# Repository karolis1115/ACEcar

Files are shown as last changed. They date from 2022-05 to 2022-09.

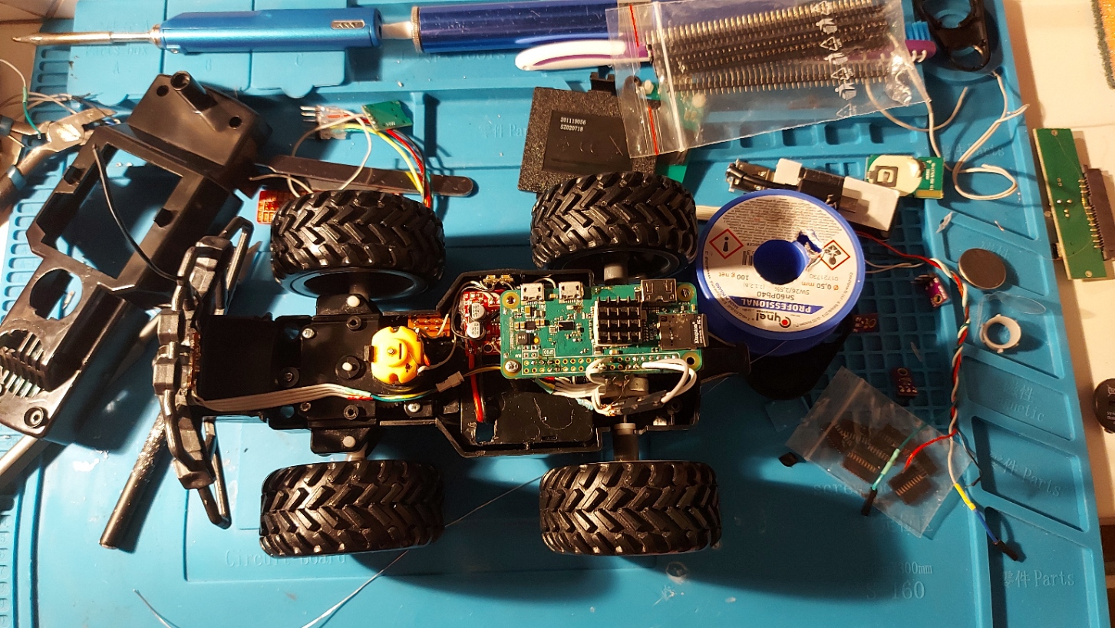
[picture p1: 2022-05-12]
Pictures and videos/20220318_200529.jpg

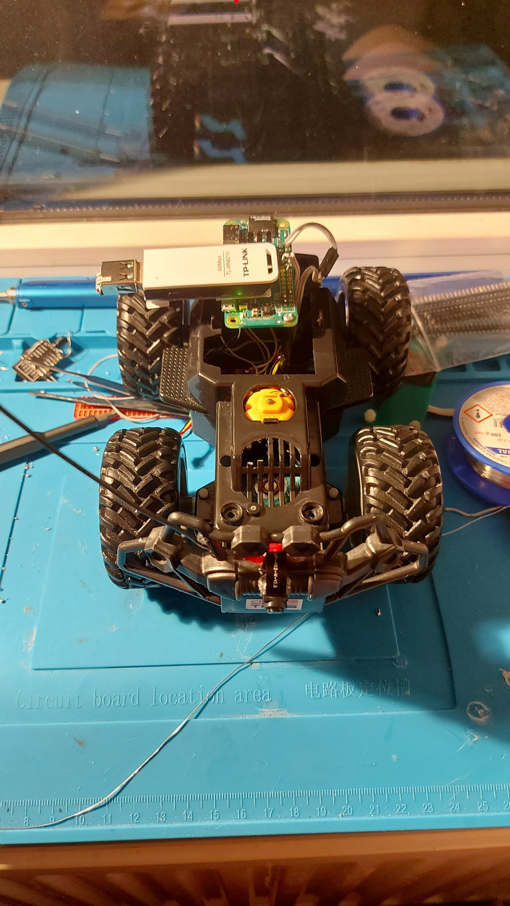
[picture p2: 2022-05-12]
Pictures and videos/20220318_201231.jpg

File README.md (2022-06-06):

# ACEcar
Saxion University of Applied Sciences Project System 2022 ACEcar repo. 

# Team members
- Miguel Pérez Hernández: 524262
- Karolis Juozapaitis: 517546
- Jurijs Zuravlovs: 440882
- Dmytro Taras: 516824
- Tarik Mandic: 523830

# Goal
To make an autonomous car that follows a line and avoids obstacles using a camera (Plan B is to use an ultrasonic sensor and light sensor array).

# What is what
- ACEcar - Main folder where main code is
- Altium files - Schematics, PCB, Gerber and other files
- Arduino test files - Files for testing different functions whre an arduino is required.
- Component sktetches - Component 3d models and sketches
- Documents - Files such as Reports and project plans and so on
- PC test files - Files for testing different functions for pc side
- Pictures - Project pictures and so on
- Raspberry pi setup - Text files that contain commands + config strings to prepare  the raspberry pi to funtion correctly for the desired requirements
- Raspberry pi test files - Files for testing different functions for pi side.

# Raspberry Pi pin configuration
- Monster Moto Driver
  - INA- 5
  - INB- 6
  - Drive (PWM1)- 12
  - Steer (SPWM)- 13

- UART
  - UART TX- 14
  - UART RX- 15

- 8x IR Line Tracking Module
  - IR- 16
  - D1-D8 -> ADC

- ADC0,1
   - SPI: 7, 8, 9, 10, 11
   - GPIO 7- CS1
   - GPIO 8- CS0

- Ultrasonic
  - Trig- 20
  - Echo- 21

# Sources
  OpenCV- https://github.com/opencv/opencv

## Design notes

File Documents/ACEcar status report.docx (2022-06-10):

ACEcar status report

This document contains a list of explanations on what has changed since the 2022 Project system race.

# Electronics

## Camera and/or cable

During the race after the car stopped video feed was lost, attempt to reestablish video feed was unsuccessful, upon closed inspection camera is missing components, due to the stress that the cable was it is also possible that the cable was damaged (however multimeter did not find any broken connections)

## Servo motors

During the development of the car, we had to replace the servo motor, the broken one is included in the box.

## Main board

for demonstration and race a PCB was not used, all connections were made manually with headers and wires, this is no longer the case as the Ordered PCB has been received, soldered and tested and is working fine after a small modification (added a capacitor to servo power pin due to voltage spikes triggering buck converter safety and shutting down the system).

P.S. Components and wires used before are contained in the box

# Cosmetic

## Frame

During the race the frame was damaged, the front bumper and back was damaged, however our team quickly repaired the broken areas and were mostly able to restore the car to its original glory.

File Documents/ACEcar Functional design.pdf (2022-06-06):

# Functional Design (FD)

# Project: Autonomous Race car

# Company: ACEcar

Place, date: Enschede, 12th February 2022

Drawn up by: Jurijs Zuravlovs
| Dmytro Taras Karolis Juozapaitis Tarik Mandic Miguel Pérez Hernández
Version: | 1.1

Drawn up by: Ali Yuksel

Place, date: | Enschede, 4.03.2022
Prepared by: | ACEcar
| Miguel Pérez Hernández | 524262 | 524262@student.saxion.nl
| Tarik Mandic | 523830 | 523830@student.saxion.nl
| Karolis Juozapaitis | 517546 | 517546@student.saxion.nl
| Dmytro Taras | 516824 | 516834@student.saxion.nl
| Jurijs Zuravlovs | 440882 | 440882@student.saxion.nl
Version number: | [1.1]
Clients: | A. Yuksel, A. Fiselier, Y. Kasemsinsup

Functional Design | version no: | iii

## Table of Contents

Functional Design | version no: | iv

## I. List of figures

Figure 1 Project management | Error! Bookmark not defined.
Figure 2 XKCD graph: walking back to my front door at night | Error! Bookmark not defined.

Functional Design | version no: | v

## II. Abbreviations

SBC
DSP | Digital Signal Processing
FFT | Fast Fourier Transform
TL;DR | Too long didn’t read
SBC | Single Board Computer

Functional Design | version no: | 1

1 Introduction.

The goal of the project is to build a car which will be follow a line. The car is moving due to hardware and software interweaving. Final product is a fully autonomous car which is following the line. The main idea is to use a sensor which takes the light and due to processing the car moves forward by the line. If the line turns the processor which see that the line is turned rotate the wheels and making the car to drive in a certain direction.

Goal of this document is to show the functional design of this project explain some basic ideas and show the concepts of a car. In this document description of a software and hardware part is provided below. Also, this document provides a requirement analysis and electronics part of the project. Therefore, the concepts and management also provided. All information this document includes can be found above.

## 2 Analysis of requirements

Requirements settled by stake holder

Requirement | Approach
1. Ride autonomously. | Create a program that will guide itself with the response of the sensors data
2. Work for at least 30 minutes. | Make sure by calculation and measurements the electric features and specifications that it will perform to that standard.
3. fit in a box of 400mm x 250mm x 200mm. | Create a model of the car respecting this dimension
4. Follow the track line (20mm). | Have sensors in order to track the line
5. Stop at the end of the track. | Figure out a way to know when the car reaches the end of the line and tell the code to terminate the program
6. Avoid obstacles. | Include sensors to have feedback if an obstacle is found in its path and be able to respond to it with an appropriate action (For ex: drive around the obstacle)
7. Find the track line. | Use input from sensors or a camera to find and track the line
8. have a body (3D printed separate parts). | Create a 3d model which will be possible to attach to the main body of the RC car.

Requirements settled by our team.

Requirement | Approach
1. Cost efficient | Calculate beforehand and produce a budget with a margin of price tolerance
2. Environmentally friendly project. | Make sure the parts used are as eco-friendly as possible like recycled printing polysynthetic
3. Development under our current knowledge | Know the team skills and knowledge to make sure the project is not too ambitious

## 3 Concept Principles

Morphological overview

Drive Mechanism | Front wheel drive | Rear wheel drive | Free wheel chain drive | 4x4 wheel drive
Processing platform | FPGA | Microcontroller | PLC | PC | Raspberry Pi
Sensor | Acoustic | optic | IR (Infrared)
Sensor amount | 1 | 2 | 3 | 4 | 5
Motor type | linear | Rotating DC | Rotating AC | stepper | Servo
Motor amount | 1 | 2
Storage | Battery | capacitor | Capacitor and battery
Car body | Pick-up truck | minivan | Convertible | Sports car | coupe

### 3.1 Description of alternative concepts

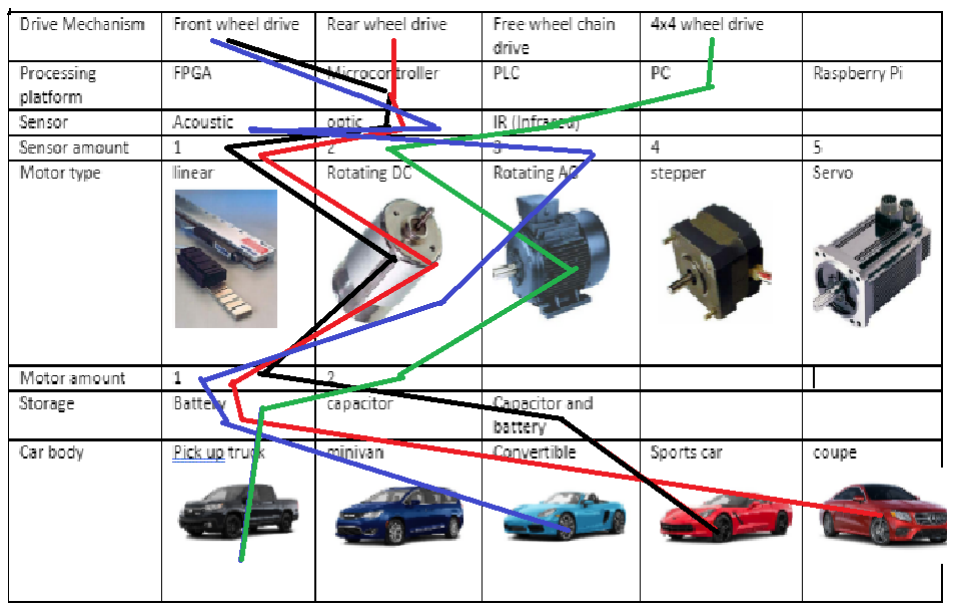
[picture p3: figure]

With the morphological overview, 4 different concepts were made.

1. Black
- Front wheel drive
- Microcontroller
- 1 Optic sensor
- 1 DC motor
- Capacitor & Battery
- Sports car
2. Red
- Rear wheel drive
- Microcontroller
- 1 Optic sensor
- 1 DC motor
- Battery
- Coupe
3. Green
- Four-wheel drive
- PC
- 2 IR (infrared)
- 2 AC motors
- Battery
- Pick-up truck
4. Blue
- Front wheel drive
- Microcontroller
- 3 sensors for either Optic & Acoustic
- 1 DC motor
- Battery
- convertible

Some comprehensive concepts:

5. Using an Arduino and a light sensor to see when it goes out of track and correct itself + an ultrasonic sensor to detect any obstacles (The simplest concept so far).
6. Using an Arduino/microcontroller with a light sensor array to detect the track and an ultrasonic sensor or rangefinder for obstacle detection/avoidance.
7. Using a raspberry pi with a camera and OpenCV to detect the track and depending on where the camera is mounted also detect the obstacles or use another distance sensor (rangefinder, ultrasonic) Demo: https://lejosnews.wordpress.com/2015/12/03/line-following-with-opencv/
8. Using a mini drone that has a camera and can stream video and be controlled over Wi-Fi for visual data which then a raspberry pi or a computer could calculate where the car and drone should drive/ fly (using OpenCV and ArUco markers) (the problem is the drone can only fly for +-5 minutes after fully charged so it would probably need to be wired up with a long but light cable) have the drone video stream and control working.

### 3.2 Comparison of concept principles

The difference between concepts 1 and 2 are the FWD and RWD and capacitor. The RWD is better because the sensor is placed in the front of the car, needing a better weight balance by putting the motor at the back. The capacitor will not be a good option for the RWD as the traction might be lost during the speed up. So, combining the capacitor with the FWD is better.

The 3rd concept is hard to do because of the processing with the PC, it is not clear how the communication will be done between the car and the PC.

The 4th concept is good, but with the Four WD, with only 1 DC motor will miss the option to add more speed to the car with the increased control that four WD allows.

### 3.3 Choice of most promising concept principle

A combination of the combination is the best.

- Four-wheel drive
- Microcontroller
- 3 sensors for either Optic & Acoustic
- 2 DC motor
- Battery
- convertible

## 4 Elaboration of chosen principle to functional design

### 4.1 Overview of functional design

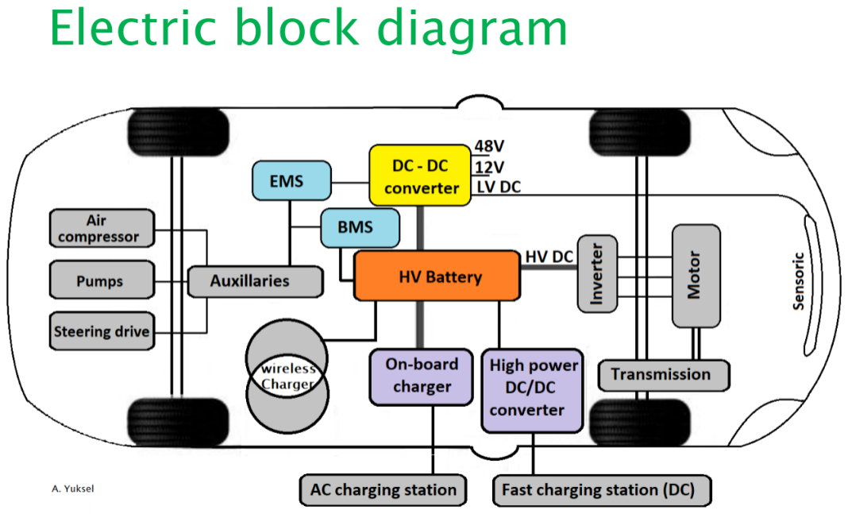
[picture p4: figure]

### 4.2 Elaboration of functional design

4.2.1 Mechanical
Base frame: ISH‑010

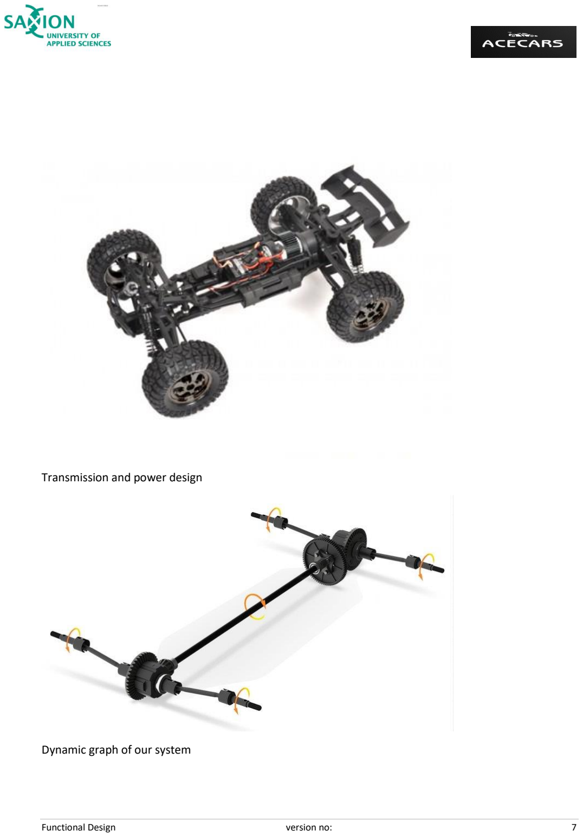
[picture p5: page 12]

Transmission and power design

Dynamic graph of our system

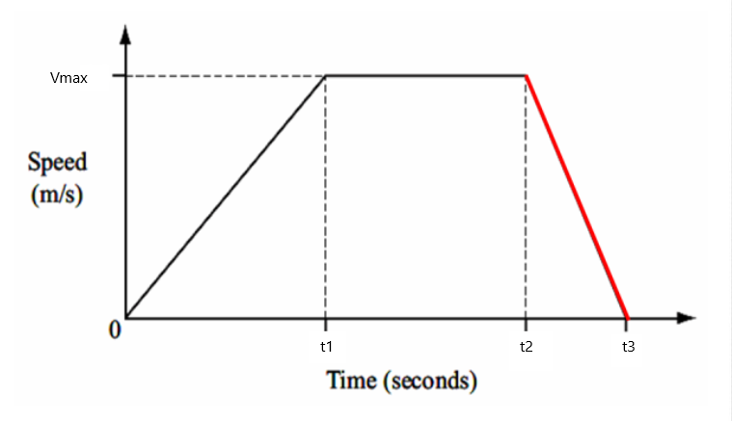
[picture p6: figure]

4.2.2 Electrical

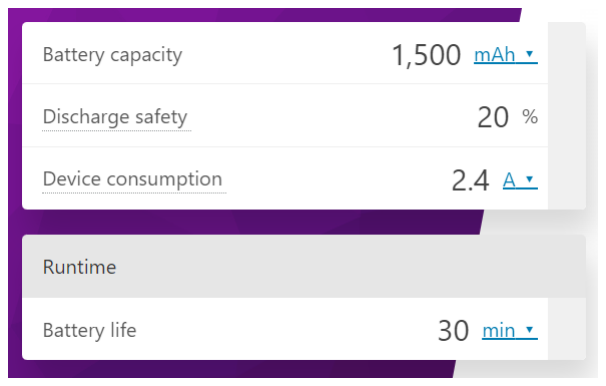
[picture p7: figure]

Battery: Li-ion 2s 1p 7.4v 1500mAh

Discharge safety: 20% (The percentage left that is considered “fully discharged” to protect the battery from over discharge may be possible to go a bit lower but a lithium-ion (Li-ion) battery cannot be discharged below 2.5 volts and a lithium polymer (Li-Po) battery cannot be discharged below 3 volts, or battery damage will occur!).

Without Risking over-discharge, we could draw 2.5A continuously to get 30 minutes of power (if discharging 80% of the battery’s capacity)

Voltage conversions:

- Battery charger ->7.4v Li-Po
- 7.4v Li-ion -> Step-down converter (5v, 3.3v, …)
- 7.4v Li-ion-> Motor driver-> Motor(s)
- Step-down converter 5v-> Raspberry Pi, servo motor, Arduino, Camera, sensors…
- Step-down converter 3.3v-> Sensors

4.2.3 Electronic
- If we choose PC, we’d need to find a way to communicate control data and sensor/ video data between the car and PC. Potentially requiring a raspberry pi anyway. This might be a good option if we’re going to need quite a bit more processing power than a raspberry pi can provide.
- If we choose a raspberry pi or similar single board computer everything could be connected locally, and we’d interface with the SBC through Wi-Fi or Bluetooth using SSH (Secure Shell Connect)
- If we use an Arduino (Meaning we’d only use sensors) we wouldn’t need any way of wireless communication since the Arduino communicates through a USB to Serial chip meaning a USB cable is all that is needed to communicate with it and upload code, we could use a button to start the car or simply add a delay from when the battery was connected.
- Using a Camera for visual data would allow to use a single sensor (the camera) for line detection, obstacle avoidance and stopping at the end of the road. The capture rate would depend on the camera and the processing power.
- Using a light sensor array would make it simpler to implement everything but would also require the use of a distance sensor (ultrasonic, laser ranging (ToF), button…)

4.2.4 Software

- Actor – Critic algorithm for self – driving cars.
- In image processing, line detection algorithm - the Hough transform and convolution-based techniques.
- Architecture diagram with modules and interfaces.

Software Block diagram [1]

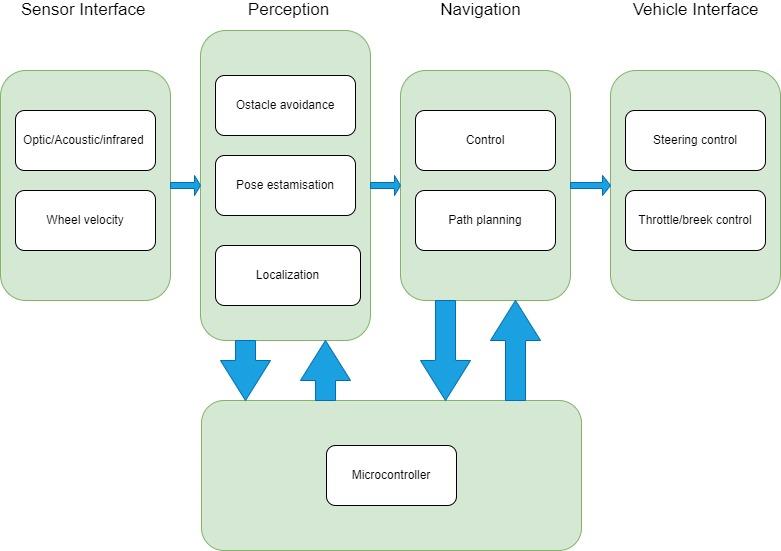
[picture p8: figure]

System states plus state transition diagram.

•
- Interrupts.

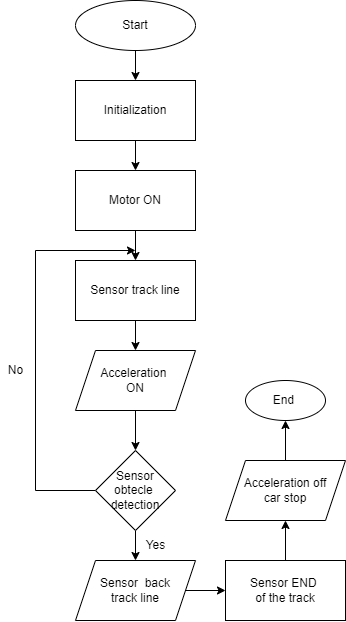
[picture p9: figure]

- Programming language and environment.
- C++, python, or C.
- Arduino IDE, Visual Studio Code, CLion.
- Minimum required 3.20(CLion)

### 4.3 Functional design integration

Safety:

- The most dangerous part of the car is the battery. If a lithium-based battery experiences damage it could potentially lead to a serious fire or explosion hazard. Battery reinforcement must be considered to ensure the safety of the car and the user in case of damage.

Speed:

- AceCar’s current goal is to complete the track in under 1 min.

Accuracy:

- The car should measure the distance of the obstacle and find a way to avoid it. Typically, an ultrasonic sensor will be a good fit for this problem (Other options exist).
- The car should be able to follow the white line without swinging side to side too much or it will reduce the speed.

Cost:

- With the provided parts the goal of an autonomous self-driving car simply cannot be achieved thus extra parts will be required. Depending on the parts used the price will vary greatly.
- The base budged is around 50€ however if provided with satisfactory arguments the budged limitation may be lifted.

Maintenance:

- DC motor: The provided motor is a “brushed” DC motor meaning as time goes on the carbon “brushes” will wear out and will typically require replacing the whole motor or replacing the brushes if the motor has such capability.
- Li-ion battery: The battery is considered a consumable and will lose its capacity bit by bit and one day will require replacing it.
- Gears: It is possible for the gears to break or wear out thus requiring replacements.

## References

Number | Author(s) | Title
[1] | R. Gandhinathan | ROS Robotics Project (2019) (https://subscription.packtpub.com/book/hardware-and-creative/9781783554713/10/ch10lvl2sec91/software-block-diagram-of-self-driving-cars)
[2] | Yong, Jia Ying, | A review on the state-of-the-art technologies of electric vehicle, its impacts, and prospects (2015) (https://www.sciencedirect.com/science/article/abs/pii/S1364032115004001)
[3] | Abhishek Gupta (https://www.ncbi.nlm.nih.gov/pubmed/?term=Gupta%20A%5BAuthor%5D&cauthor=true&cauthor_uid=33105863) | Policy-Gradient and Actor-Critic Based State Representation Learning for Safe Driving of Autonomous Vehicles (2020) (https://www.mdpi.com/1424-8220/20/21/5991)

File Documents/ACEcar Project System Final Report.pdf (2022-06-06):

Project System: Final report

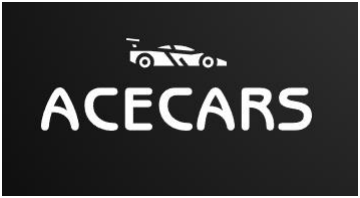
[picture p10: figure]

Autonomous Race Car

Place, date: Enschede, 24th May 2022 Drawn up by: Jurijs Zuravlovs
| Dmytro Taras 516824
| Karolis Juozapaitis
| Tarik Mandic
| Miguel Pérez Hernández
Version: | 1.2
Group Nr: | 25

Place, date: | Enschede, 12.02.2022
Prepared by: | ACEcar
| Miguel Pérez Hernández | 524262 | 524262@student.saxion.nl
| Tarik Mandic | 523830 | 523830@student.saxion.nl
| Karolis Juozapaitis | 517546 | 517546@student.saxion.nl
| Dmytro Taras | 516824 | 516834@student.saxion.nl
| Jurijs Zuravlovs | 440882 | 440882@student.saxion.nl
Version number: | [1.2]
Clients: | A. Yuksel, A. Fiselier, Y. Kasemsinsup

Table of Contents

Abbreviations

MoSCoW | Must, Should, Could, Won’t have
PCB | Printed Circuit Board
CV | Computer Vision

List of figures

Figure 14: Body Design 26

Introduction

Background

This project started at the beginning of February, to make and design an autonomous racing car. We at ACEcar, have worked hard and long to create a satisfactory product for out Stakeholders at Saxion University. To design something new and innovating and to combine our strengths to win the Saxion E-Race. This report will show our design and work method used to create the future winner of the Saxion E-Race.

Objectives
The MoSCoW method operates by splitting the clients’ requirements into the most important ("Must"), all the way down to additions which would be nice to have, but are not necessary ("Could"), while also agreeing on things which are not feasible due to either timing issues or just not enough manpower ("Won’t have").

Must:

- Ride autonomously.
- Follow the track line (20mm).
- Stop at the end of the track.
- Avoid obstacles.
- Find the trackline.

Should:

- Fit in a box of 400mm x 250mm x 200mm
- Drive for at least 30 minutes continuously
- Have a body (3D printed separate parts)

Could:

- Accelerate to the maximum speed.
- Automatic return to start for charging or restarting mission
- Have a drone that follows the car autonomously to either give visual track data or to just record the car driving
- Make the car faster with either better or multiple motors
- Process the car through the network.
- Have a light that indicates whether they oversee the vehicle.
- Manual control through either a physical remote or laptop/phone/tablet

Won’t have:

- Solar powered batteries (which would contribute to sustainability and the renewable energy movement)
- More than two engines or batteries.
- An overkill engine
- Off road tires.

Methodology

The methodology we will use to develop our project is the V-model which we can separate into some steps.

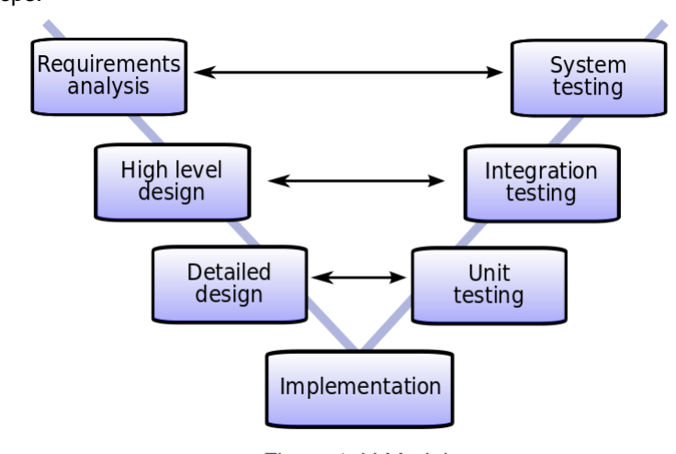
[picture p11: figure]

Figure 1: V-Model

- REQUIREMENT ANALYSIS.
- Looking for what the user is requiring (behavior and specification of the system). To structure the user requirements, we will use MoSCoW method. Look at the technical requirements (what components do we need).
- HIGH LEVEL (FUNCTIONAL) DESIGN.
- Figuring out how to create the system, trying to describe what steps the machine will take for different inputs. How the circuit is going to respond to the procedure.
- LOW LEVEL (TECHNICAL) DESIGN.
- Creating a visible idea of the project (via schematic, flowcharts and drawings) and simulating if it works. Creating a more specific flowchart of how individual systems work.
- IMPLEMENTATION.
- Making the result (PCB printing and loading code to Arduino).
- TESTING.
- For each of the steps above we will have to do a test to detect and solve possible bugs and check if the project is meeting all the requirements.

Safety

For this project there are several things which should be followed in order to succeed and finish project in time without any delays. The safety principles can be divided into hardware safety, software safety and team safety. For the hardware safety, the current and voltage limit applies to a hardware to prevent it’s burning or even exploding. The detailed limit could be found in technical design part, at the electronics. For the software safety some unit tests were done to check if the code works properly, and it won’t have any bugs during the race. Also, tests if the applied software works good with hardware in order to prevent unexpected errors during the race. Backup plan was considered If something could go wrong, and the group lost everything or just a piece of something. For the group safety, some basic safety methods, which would been followed during work with electronics and 3d printers.

Structure

The following part of the report includes the execution of the assignment, which contains:
- Project Objectives
- Project activities
- Project boundaries
- Quality assurance
- Project organization
- Planning
- Costs and benefits
- Risk analysis

After that comes the Functional Design, Technical design, Result, Conclusion and Recommendation, References and lastly the Appendix.

Execution of assignment

Project Activities

Project setup
- Project plan.
- User requirements.
- Acceptance test plan.
System Requirements
- Functional requirements.
- Technical requirements.
- System test plan.
Functional Design (High level design)
- Concepts.
- Choosing a concept.
- Functional design concept chosen.
- Sub-system test plan.
Technical design (Detailed design)
- Technical block diagram.
- Calculating and selecting essential components.
- 3D and 2D mechanical design.
- Schematics and PCB design.
- Pseudo code.
- Module/Unit test plan.
Realisation
- Mechanical – Making components and module assembling.
- Electrical-Electronic – Making PCBs and module assembling.
- Software – module/unit coding.
Module/Unit Test
Sub-system Test
- Module integration.
- Test.
Factory Acceptance Test
- Sub-system integration.
- System Test.
Site acceptance Test
Finalization project
- Final report & Documentation.
- Personal contribution document.
- PowerPoint presentation.

Project Boundaries (scope and pre-conditions)

Start day: 11th of February 2022
End day: 26th of May 2022
Length of the project: 105 days
Budget: 50€ (Unless “ACEcar” convinces the stake holders to increase the budget) The pre-conditions that must be met for the project to have a chance of success:
- Project members each need to be assigned a role that the members will be working on (design, programming, management, electronics, etc.)
- “ACEcar” needs to decide on what technical approach will be chosen
- The preliminary design of the vehicle needs to be thought out for the prototype
- A prototype of the product needs to be made for testing purposes
- All important documents must be filled in and submitted
- The parts list must include the required parts price and links to the parts What doesn’t belong in this project:
- A website promoting our company and product
- personnel other than the ACEcar team working on the project.

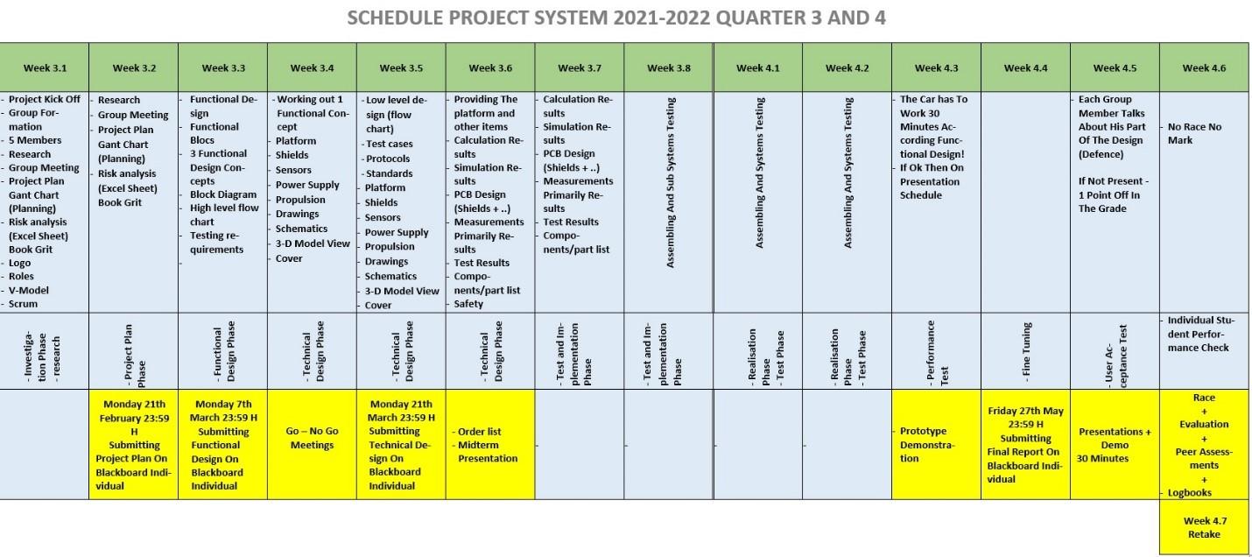
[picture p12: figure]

Figure 2: Project Schedule/Timetable

Quality assurance

The desired quality will follow the project objectives mentioned in the Introduction under Objectives.

Before the production of the product, an order list, project plan, a functional and technical design must be created and submitted for feedback. Either to improve or change the conceptualization of the product.
The quality of the product will be tested by phase tests known as, Module/Unit Test, Subsystem Test, Factory Acceptance Test and Site acceptance Test.
External advice might be requested from other parties or experts to evaluate the intermediate product/results.

Some tools that were used:

- Visual studio code.
- Draw.io.
- Altium.
- TinkerCad.
- SOLIDWORKS.
- Word.
- Teams.
- Excel.
- Python
- OpenCV

How our team thinks of Quality assurance steps.

### 1. Define quality

Quality is ambiguous, it can mean many things. For example, The Project Management Body of Knowledge (PMBOK) (https://www.pmi.org/pmbok-guide-standards) Defines quality as, “conformance to requirements and fitness of use”, ISO 9000 (https://www.iso.org/iso-9001-quality-management.html) defines quality as, “the degree to which a set of inherent characteristics fulfill requirement".
Whatever type or size of project you are managing, take the time to define the quality criteria for your current work so that your team members understand what it is, and how to reach and improve upon it.

### 2. Commit to quality

A company's commitment to quality must come from the top and be reinforced repeatedly. Unless a business views quality as its single, non-negotiable goal, workers will inevitably feel the need to make trade-offs and quality will slip.
As a project manager or leader, commit to quality, share the commitment with your staff and think about how you will handle the any conflict between your stated objective and an attractive cost-saving, short cut that compromises quality.

### 3. Stick to the project requirements!

Once you’ve defined the quality criteria and project requirements, stick to them! Balance continual project improvements with gold-plate requirements. Adding features, the customer did not request increases the potential for delays, and higher cost. Project Managers drive improvements and project quality but beware of out-of-scope extras creeping in.

### 4. Manage quality

Work with your project team to define a practical approach to managing quality, including applicable standards and quality processes. These are driven by your standards and quality processes contained in the project blueprint. (https://www.hydra.cloud/en/resources/blog/templates-vs-blueprints)

### 5. Perform quality assurance

Execute your quality management plan using the standards and processes defined in the project blueprint. Perform a quality audit to evaluate how well the team is following the plan and meeting your customer’s expectations.

### 6. Control the quality

Ensure the deliverables are correct and free of defects and focus on quality from the beginning to the end of the project. Perform inspections to identify defects. Start as early as possible; identifying and correcting defects close to the point of origin saves time and
money.

### 7. Focus on requirements

Requirements management and quality management go hand in hand. Clear, well-defined requirements lead to less rework and schedule delays. Focus on improving the requirements process—eliciting, analysing, documenting and validating them.

### 8. Follow the project processes

Follow the processes and tasks contained in your project blueprint. If you identify a more efficient way to do something, add this into the blueprint to continually improve the processes. (https://www.hydra.cloud/en/resources/blog/quality-improvements-vs-the-need-for-project-efficiency)

### 9. Lessons learned

Document lessons learned (https://www.hydra.cloud/en/resources/blog/how-to-learn-from-project-experiences) after project phases and at the completion of the project to evaluate your processes and ‘bake’ all the improvements into the project blueprint and translate them to future projects. This forms part of your knowledge management (https://www.hydra.cloud/en/resources/blog/3-resons-why-having-a-knowledge-management-strategy-is-important-for-organisations) strategy: you build up a knowledge bank and use lessons learned in the last project for both existing and new projects.

### 10. Project De-Brief

The project de-brief (https://www.hydra.cloud/en/resources/blog/what-to-cover-in-a-project-de-brief) is more than a casual conversation about what did and didn’t work, it digs into why things happened (or didn't happen). A de-brief can sometimes be as painful as the project itself, especially when your project has failed, and you need to investigate where things went wrong. Rather than rushing headlong into your next project take time for a thorough de-brief with both your team and your client so that over time you continuously improve the consistency of quality in your projects and deliver more of them successfully.

Costs and benefits

Project costs:
- Man-hours, 140 hours per person.
- Main Budget 50 euros Max threshold of 10 euros
- Other facilities like space work or design tools are covered by our stake holders
Project benefits:
- Reflect on the specific Body of Knowledge and Skills of ACS and EEE
- Understand the Arduino and several Shields and Modules for data processing and control
- Do calculations, simulations and designing circuits for this Project
- Do electrical and mechanical measurements and software coding
- Do electrical and mechanical test measurement
- Implementing several electronic modules
- Building autonomous driving electrical Racing Car
- Work in a structured way to become a solution for a defined problem
- Experience Teamwork with individual responsibilities and work in a structured way
- Organize a scheduled group and supervisor meeting
- Report technical information with specific software tools
- Do an Oral presentation with PowerPoint for a select Audience
- Perform respectively as a chairman and as a secretary in the group meetings
- Convince the Graders of your individual knowledge and skills improvement (reflection)

Risk analysis

The risk analysis was done by filling in the risk analysis table in the Appendix.

After gathering all the information, our team scored a pretty good score in risk analysis, meaning we can successfully continue our work. There are also many more risks that we take care of, and our management team analyses all of them to try to better succeed. To summarize, all risk assessment methods are considered the foundation for all operational risk assessment methods. Our strength of effectiveness is based on our teams' simplicity and ease of use, acting as quickly as possible on the numerous risks that need to be assessed.

1. Some members could be slacking off.

Split the work evenly and democratically. group meetings to learn about problems and solve them together. If some team members refuse to work together or refuse to participate in any type of work, the team has no choice but to vote them out of the team and project.

2. Not enough manpower or time to fulfil all the client’s expectations.

In order to ensure that all the client’s expectations are met, it is important to thoroughly plan out the workload between group members - if something seems too taxing to be implemented then the client is alerted beforehand, so as not to deliver a subpar product.

3. A mistake in the hardware or software.

By having everyone from the group check both the software and hardware portions of the project, we can ensure a high standard of value is upheld. Although this would take some more time, it ensures that everything the group does is done correctly, and as Linus’s law dictates: “given enough eyeballs, all bugs are shallow (Raymond and Torvalds, n.d.)”.

4. Failure of Components.

To avoid future errors in the system or mis failure of components, we would like to have some extra pairs of sensors, wires, LEDs, and parts to guarantee the quality of our product.

5. Poor management.

A project's success is dependent on good management. A good leader is supposed to have good communication and interaction with the team. Therefore, high standards are always set for the project manager.

6. Poor productivity.

To avoid low productivity among team members, the team leader should exercise strict control. In addition, there could also be a spread of the workload between the other members to avoid this risk.

7. Technical risks.

There may be a technical issue like a device that is not working, and this will be a risk as one of the members is out of the project unofficially. A way to solve this problem is to borrow this member a device or he himself finds one.

8. Bad timing.

To avoid this software development risk, apply agile methodologies, ensure the maximum involvement of all team members in planning and estimating, receive feedback at all stages, starting from the earliest ones, and involve the owner or stakeholders.

Functional Design

Functional design of this project explains some basic ideas and show the concepts of a car. Description of a software and hardware part is provided below. Also, here provided a requirement analysis and electronics part of the project. Therefore, the concepts and management also provided. Below, the following will be found.

- Block diagram and description
- System operation Description
- System specification
- Test procedures

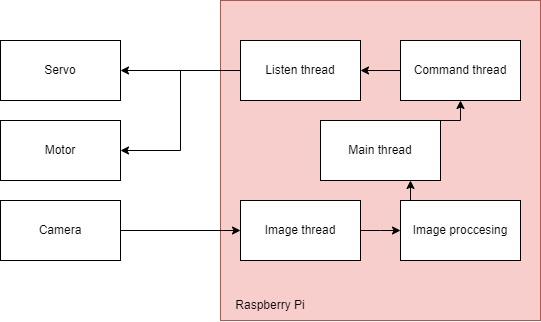
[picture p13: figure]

Figure 3: Architecture overview

The architecture of the car is built that the main computer for processing was Raspberry Pi, which consist of few threads such as image processing, main thread, and the command thread. The image thread takes data from the camera and sends it to the processor. Depending on the data raspberry pi provide the output for the servo which is used to rotate the car, and the motor, which is for speed.


Figure 4: Software Block diagram

Software block diagram shows the subsystems of the project. Each of the subsystem represented below represent a function the car follows.

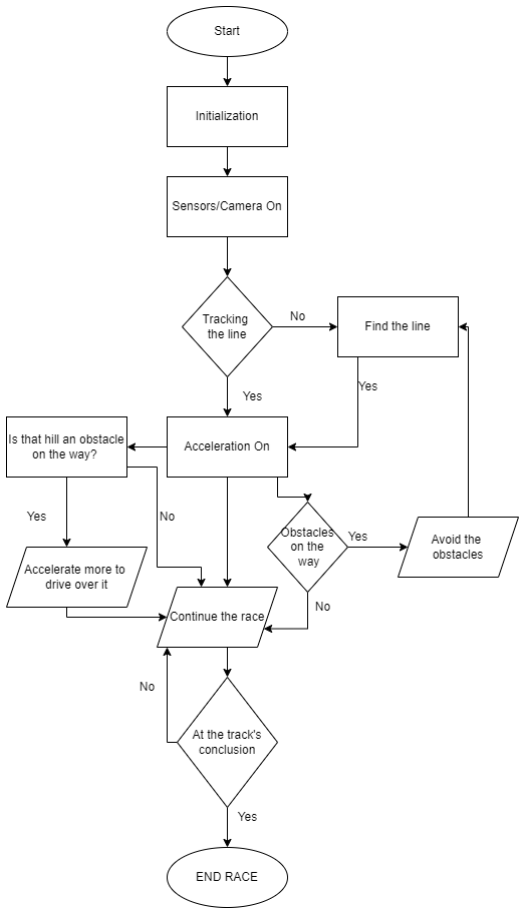
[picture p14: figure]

Figure 5: System states plus state transition diagram

State transition diagram shows exactly on which stage the car during the race and how the stages changes during the race.

Technical Design

Project files can be found on the GitHub repository: https://github.com/karolis1115/ACEcar

Technical Design Document for use by Ace Cars Projects provides guidance which is intended to assist the relevant management and technical staff, whether client or supplier, in producing a project‑specific Technical Design. It is presented as blocks of software, electric and electronic diagram which includes software and hardware part of the project.

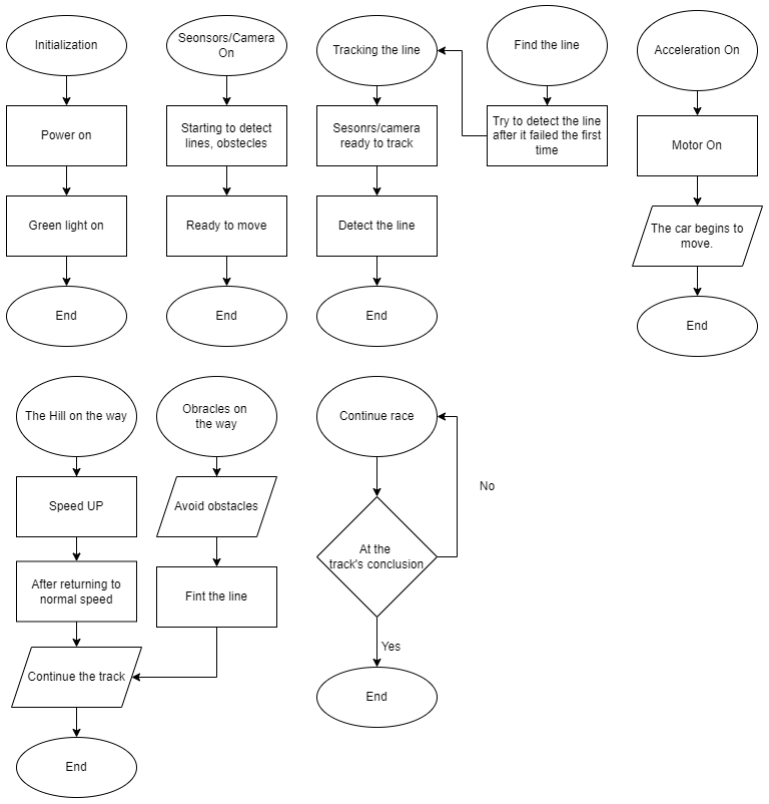
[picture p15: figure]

Figure 6: System Diagram

The above diagram shows all the steps the code goes through to complete the mission. From start to finish. Line following, obstacle avoidance, end detection.

Electrical

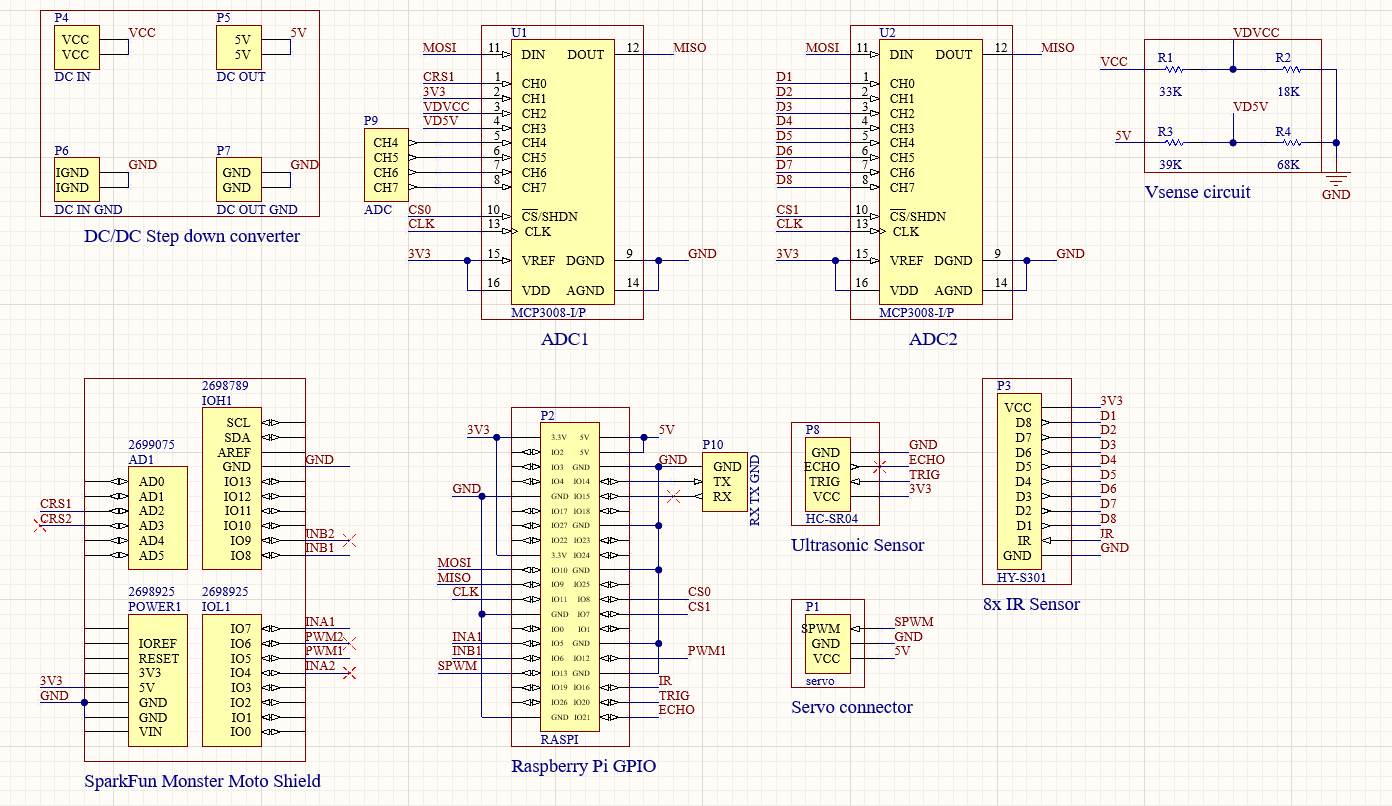
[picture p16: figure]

Figure 7: Electric circuit schematics

The schematic above depicts every part of the electrical and electronic system. From power to logic.

- DC/DC Step down converter- Used to step down Battery voltage down to 5V
- ADC1(2)- Analog to Digital Converted IC for voltage, current sensing and 8x IR sensor.
- Vsense circuit- 2 voltage divider to convert battery voltage and 5v to voltage levels suitable for measuring using the Raspberry pi and ADC.
- SparkFun Monster Moto shield- Pins for the motor driver in Arduino form factor
- Raspberry Pi GPIO- Raspberry pi’s IO and power (5V 3V3)
- Servo Connector- Connector for steering servo motor
- Ultrasonic Sensor- connector for Ultrasonic sensor (Plan B)
- 8x IR Sensor- IR light sensor module for line detection (Plan B)

Plan B- In case the use of a camera and image processing libraries fails to achieve the desired goal ACEcar has decided to implement a backup approach to achieve its goals. In case of failure to achieve Plan A (Camera + Image processing) The team will use an IR line detection module and ultrasonic distance sensor to achieve said goals.

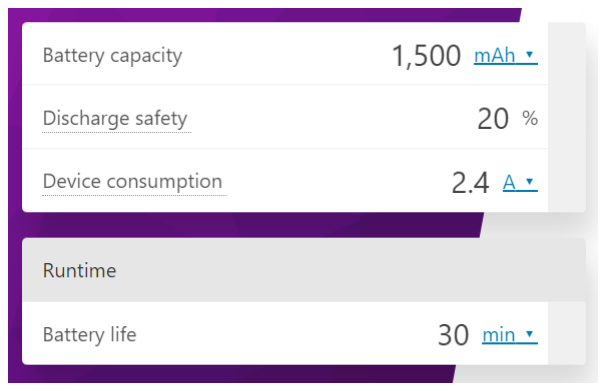
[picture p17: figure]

Figure 8: Battery Duration

Because the car has to be operational for at least 30 minutes on battery power this calculation shows the max current the car can draw to last 30 minutes (while leaving 20% battery to not over discharge it)

Battery: Li-ion 2s 1p 7.4v 1500mAh

Discharge safety: 20% (The percentage left that is considered “fully discharged” to protect the battery from over discharge may be possible to go a bit lower but a lithium-ion (Li-ion) battery cannot be discharged below 2.5 volts and a lithium polymer (Li-Po) battery cannot be discharged below 3 volts, or battery damage will occur!).

Without Risking over-discharge, we could draw 2.5A continuously to get 30 minutes of power (if discharging 80% of the battery’s capacity)

To get the actual battery duration of the car, measurements were done and some calculations.

Power_max = Battery capacity * Voltage = 1.5 * 7.3 = 10.95 Wh

Battery duration = Pmax / Pmeasured

Voltage | No load(current) | Battery duration(hours) | Max load | Battery duration(hours)
7.3 | 0.9A | 1.667 | 3.2A | 0.47
PWM 70 | 0.75A | 2 | 2.9A | 0.52

Voltage conversions:

- Battery charger ->7.4v Li-Po
- 7.4v Li-ion -> Step-down converter (5v, 3.3v, …)
- 7.4v Li-ion-> Motor driver-> Motor(s)
- Step-down converter 5v-> Raspberry Pi, servo motor, Arduino, Camera, sensors…
- Step-down converter 3.3v-> Sensors

Electronic

ACEcar decided to use a Raspberry Pi microcomputer to communicate with a PC. The Raspberry Pi will transmit video data using a camera connected directly to the raspberry pi’s camera port. It will send the video data to the PC, where it will then use OpenCV to process the frames (detect the track, obstacles, and end). The PC will then send back control data to the Raspberry Pi, i.e., speed, steering, direction. ACEcar has figured out a way to transmit smooth video through the network without much latency.

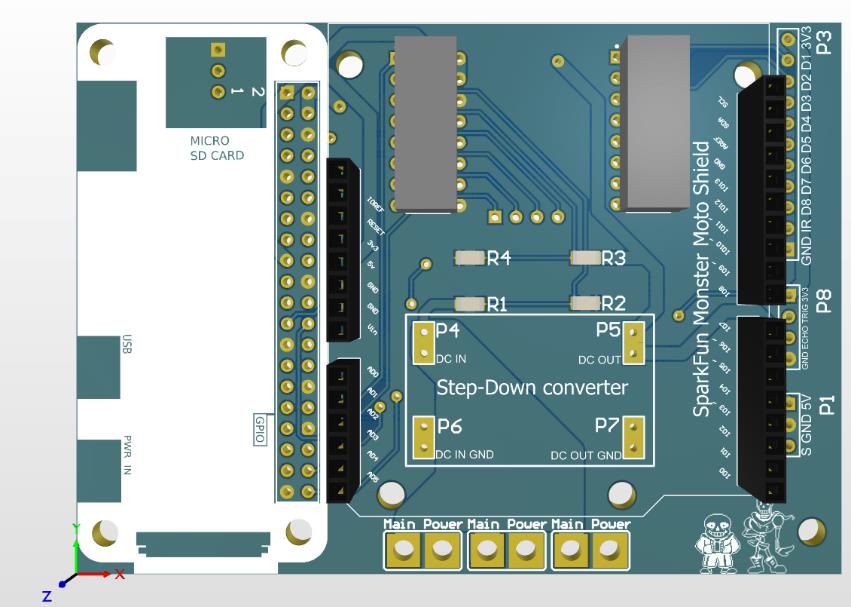
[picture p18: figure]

Figure 9: PCB Layout (top view)

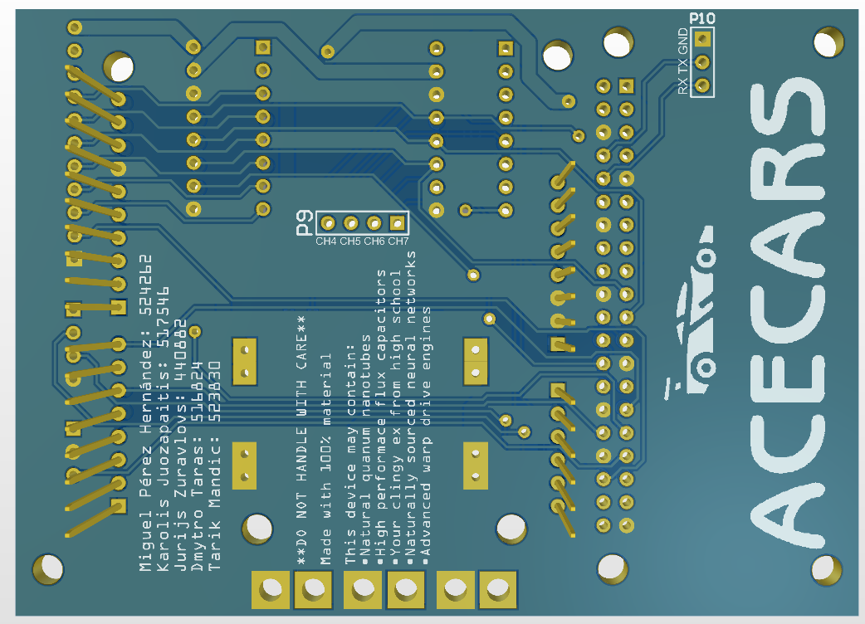
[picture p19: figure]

Figure 10: PCB Layout (bottom view)

ACEcar has decided to go with a Custom-made Printed Circuit Board (PCB). This approach has many advantages:

- The car can be made much more compact due to there being little to no wires.
- The PCB makes connections more reliable and robust since components are being soldered directly to the PCB.
- Troubleshooting and problem finding can be done much easier since every connection stays at the same place and with the help with the schematics a fault or error can be found much more efficiently.
- Using a PCB can also save space and make the inside look nicer.

Software

Project files can be found on the GitHub repository: https://github.com/karolis1115/ACEcar

The idea is to find the path using colour detection or edge detection and then get the curve using a summation of pixels in the Y direction, i.e., a histogram. We split the task into five different steps. This includes thresholding, warping, histogram, averaging, and display. The main idea was to use only OpenCV because it has a lot of essential information and possibilities which are used even in real cars.

- Servo turning algorithm, Initialization of servo, DC motor, batteries etc.
- Appendix B.

Low level flow chart.

- Appendix A.

Software block diagram.

- Appendix C.

Architecture Overview

- Python 3.x
- OpenCV
- Raspberry Pi
- Visual Studio Code.

These testing methods were conducted in order and include:

- Unit testing
- Integration testing
- System testing
- Acceptance testing
- Our team also first split the code into many subtasks, each of which was tested separately. After passing all the subtests, we start to put everything together and test it all together again, fixing all bugs or wrong code.
- Simply use the colour detection to find the path.

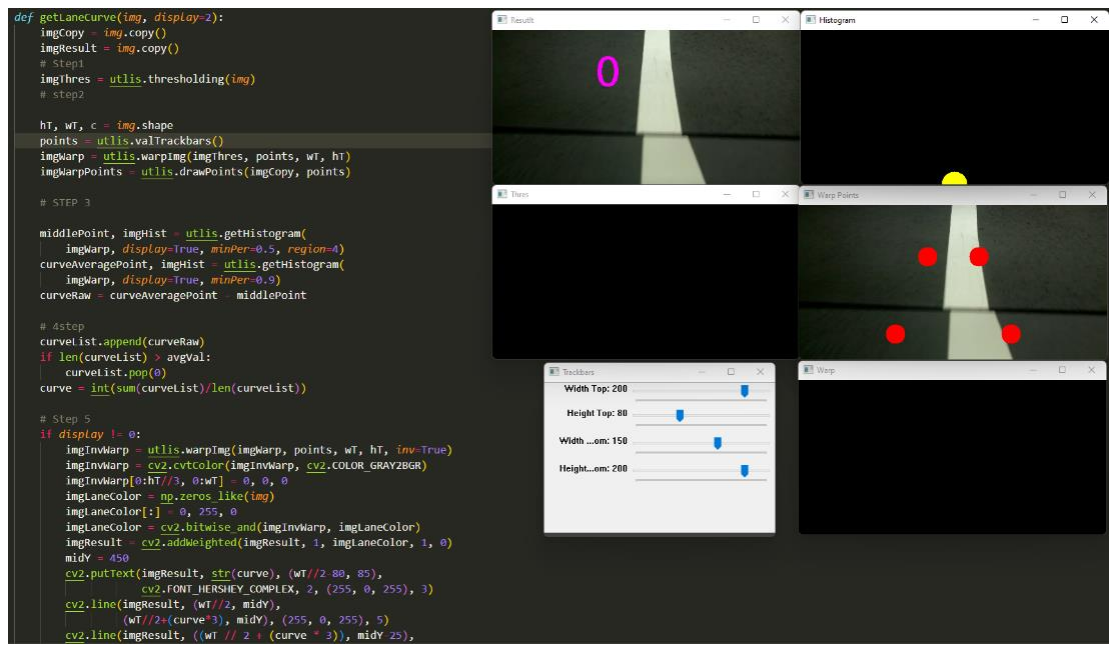
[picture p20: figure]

Figure 11: Detect white colour

- In this case, our team simply converts the image to HSV-colour space and then uses a colour range to find the proper colour. This colour could be found using the colour picker script. Which was tested on video from the race track.

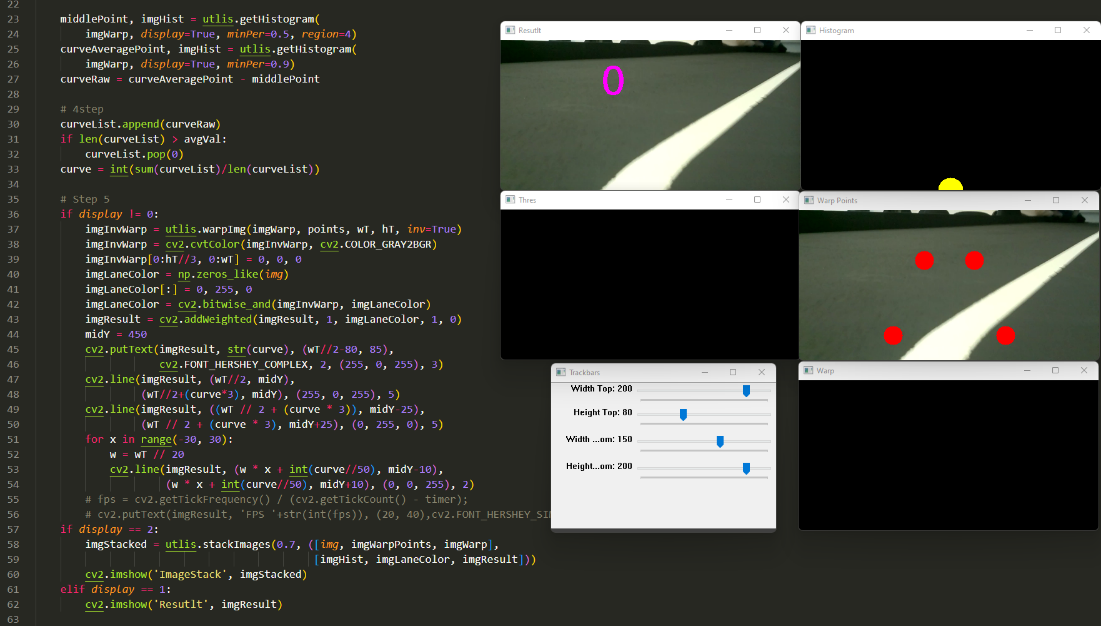
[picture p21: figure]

Figure 12: Finding the curve

- The most important part is to find the curve in our path. For the curve, the summation of pixels is used. Given that our warped image is now binary, it has either black or white pixels, we can sum the pixel values in the y direction.
- To find the center of the base, which will give the center line, and then compare the pixels on both sides.

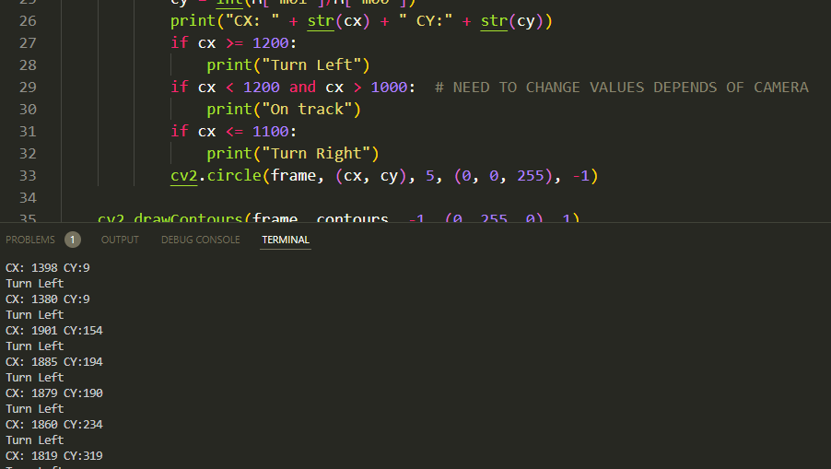
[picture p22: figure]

Figure 13: Calibration

- All the test procedures were completed in order to make the code simpler and more accurate. There was also a camera calibration and proper colour detection for all scenarios.

Mechanical - Physical Design

For the physical and mechanical parts of the project, we performed some calculations, estimating final velocity acceleration, etc. This is especially important to ensure the correct functioning of our design and to ensure its efficiency. Values like the mass or some forces we could calculate were necessary for making these calculations. Knowing the parameters, we could already create our body design and mountings for our components.

We first made a 3D scan of the base model RC car given to us. This way, we could more efficiently make certain that the design we were going to create was compatible with the already existing model. You can see a picture of this below.

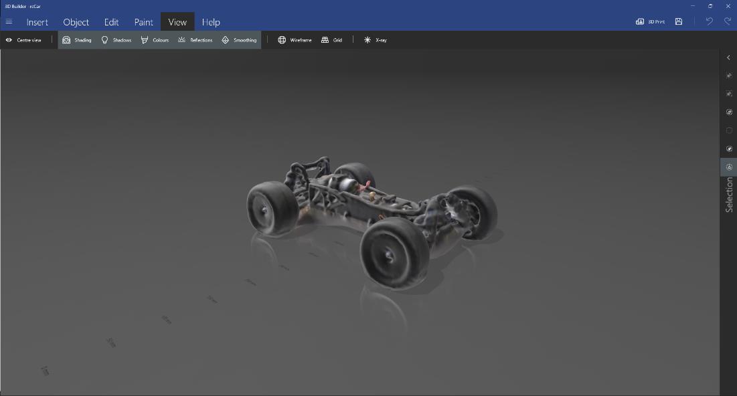
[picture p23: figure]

We also made some 3D models of the electronics we were going to use to make certain the size and the measurements were exact. Below you will see the PCB and our ultrasonic sensor, listed in the same order.

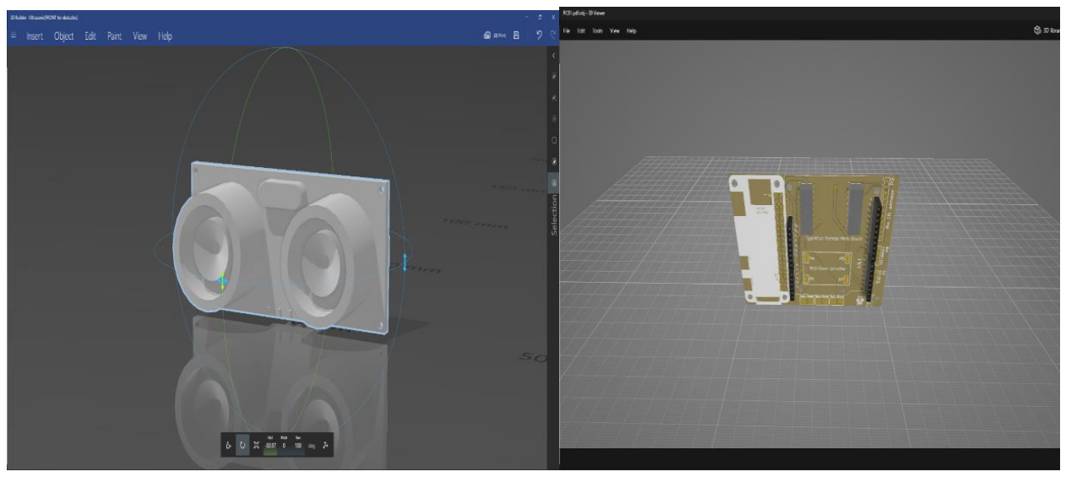
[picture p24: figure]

Following that, we started to develop our design on top of these things, ensuring that the car's mechanics worked properly.

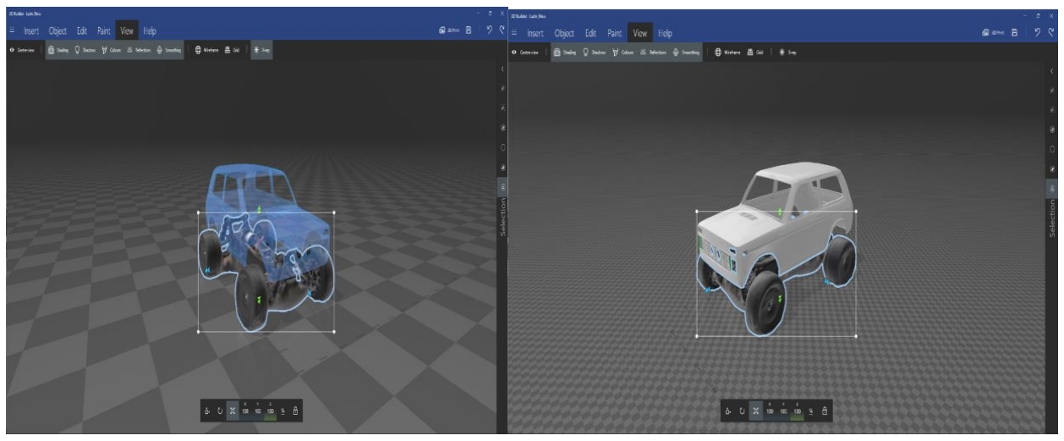
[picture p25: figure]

As you can see, the body design fits perfectly with our base model and has space for electronics. This way we are more efficient and won't have to repeat the printing process, which is the most time-consuming. For printing, we had to split our design in two because one printer alone could not handle the entire print. And after printing, we had to take our models and join/perfectionate them, taking off supports and sticking them together.

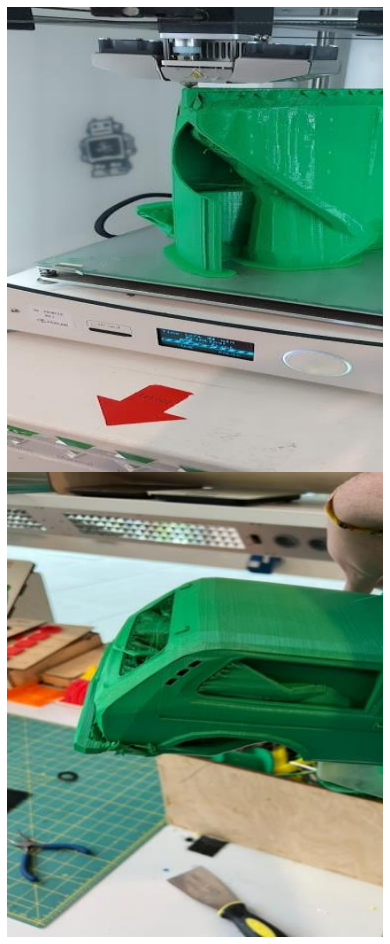
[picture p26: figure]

Conclusion


To conclude, the AceCars team has created an autonomous racing car which was the main goal of the project. By the end, the car follows the line on track and shows a good result in speed. The project was hard but avoided all the risks and followed all the planning, the team performed good. Some of the design decisions was changed during the project such as 3d model of the body of the car and neural network to control the racing to a better one and were successfully involved in the project. Some software ideas were shown as impropriate during the test and were changed. The success of the project means that the following all the design ideas above will make a good racing car.

Recommendation

This was a fantastic challenge for our organisation. The entire staff was focused on making it great. By the conclusion of the academic year, we want to have built an autonomous racing car. AceCar will accomplish this by developing a truly unique product that is totally autonomous, capable of detecting the track line and avoiding obstructions. If this target is met, a brand-new product will be created that can be used in the future.

We must first acquire all the necessary information for building a racing automobile. We'll need to build a model, link all the necessary elements, make a customized 3D print, and programme it to do the job.

To meet all our objectives, we must take all electrical measurements, calculate colours, and construct a car appropriately. The team used a variety of measurements to determine how many resources were required and what needed to be done.

The most important task is to stick to the strict plan in order to achieve the greatest possible result.

References

[0] https://github.com/karolis1115/ACEcar - ACEcar GitHub project repository.
[1] Grit, R. (2010). Project management. Noordhoff Uitgevers.
[2] Bruyninckx, H. (2008, 7 March). File: V-model.svg. Wikipedia. Visited on 23 May 2022, from https://commons.wikimedia.org/wiki/File:V-model.svg

Appendix

Risk analysis

Risk | Value | Factor | Weight | Total risk
1. Estimated duration of the project? | 0–3 months 0 3–6 months 4 - 6+ months | 0 1 2 | X4 | 0
2. Does the project have a definite deadline? | No Flexible Yes | 0 2 4 | x4 | 16
3. Is there sufficient time to complete the project within the set period? | more than enough enough not enough | 0 1 3 | x4 | 4

Complexity of the project
4. The number of functional subsectors involved? | 1 2 3+ | 0 1 3 | x4 | 12
5. The number of functional subsectors that will make use of the outcomes? | 1 2-3 4 | 0 1 2 | x2 | 4
6. Is it a new project or one that has been adapted? | minor adaptions major adaptions new project | 0 2 3 | x5 | 15
7. To what extent do the present authorisations have to be adjusted? | Not minor extent medium extent major extent | 0 1 2 3 | x5 | 5
8 Are other projects dependent on this one? | No yes, though the deadlines are not tight yes, and the deadlines are tight | 0 1 3 | x5 | 15
9. What sort of reception are the users likely to give it? | Enthusiastic noncommittal interested | 0 1 2 | x5 | 5
10. Has the project been divided up into phases and is progress dependent on the coordination between them? | No a little strongly | 1 2 3 | x3 | 15

Project group
11. Where do the project workers come from? | mainly internally partly internally mainly externally | 0 1 3 | x4 | 4
12. Where is the project located? | 1 location 1 to 3 locations more than 3 locations | 0 1 2 | x2 | 0

13. The number of projects taking up more than 80% of peak hours? | 1 – 5 5 –10 5 – 10+ | 024 | x5 | 10
14. The balance between subject experts and project experts? | Good Average unfavourable | 024 | x5 | 0
15. Are the users involved in the project? | to a large extent to a reasonable extent to a limited extent | 013 | x3 | 9

The project management
16. Does the project management team have any knowledge of the subject? | a lot a reasonable amount little | 024 | x3 | 6
17. Does the project management have any knowledge of how to plan a project? | a lot a reasonable amount little | 024 | x3 | 6
18. How much experience does the project manager have with projects like this? | a lot a reasonable amount little | 013 | x3 | 3
19. Do the advisers have any knowledge of the field of research? | a lot a reasonable amount little | 013 | x5 | 0
20. Do the subject experts have much knowledge of the field? | a lot a reasonable amount little | 013 | x5 | 0
21. How involved in the project are the managers responsible for it? | Very reasonably involved only slightly | 025 | x5 | 10
22. Is there any chance that the project team will change during the project? | little chance some chance big chance | 025 | x5 | 0
23. Is the project group using existing methods or creating its own methods? | only existing methods some existing methods no existing methods | 024 | x4 | 0

Project definition
24. Are the project members sufficiently aware of the problems and objectives? | yes, everybody most of them not all of them | 015 | x5 | 0
25. Is the field of research sufficiently demarcated? | yes reasonably | 02 | x5 | 10

| not clearly | 5
26. Is there sufficient demarcation between this project and other projects? | considerable reasonable insufficient | 0 1 3 | x4 | 0
27. Has enough time been reserved for coordination and decision-making? | considerable reasonable insufficient | 0 1 3 | x4 | 0
28. Are the boundaries clearly demarcated? | Yes in general most of them are not | 0 1 3 | x4 | 0
29 Are the boundaries limiting enough? | Yes moderately no | 0 2 5 | x5 | 10

Risk percentage =

score
max score

x 100% = 35%

Appendix A: Software high level flow chart:


Appendix B: Software Block Diagramm [2]:

Appendix C: Architecture overview:

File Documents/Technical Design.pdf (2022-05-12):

# Technical Design (TD)

# Project: Race car

# Company: ACE car

Place, date: Enschede, 24th March 2022

Drawn up by: Miguel Pérez Hernández
| Tarik Mandic Karolis Juozapaitis Dmytro Taras Jurijs Zuravlovs
Version: | 1.0

Place, date: | Enschede, 24.03.2022
Prepared by: | ACEcar
| Miguel Pérez Hernández | 524262 | 524262@student.saxion.nl
| Tarik Mandic | 523830 | 523830@student.saxion.nl
| Karolis Juozapaitis | 517546 | 517546@student.saxion.nl
| Dmytro Taras | 516824 | 516834@student.saxion.nl
| Jurijs Zuravlovs | 440882 | 440882@student.saxion.nl
Version number: | [0.1]
Clients: | A. Yuksel, A. Fiselier, Y. Kasemsinsup

Functional Design | version no: | iii

## Table of Contents

Table of Contents | iii
I | List of figures
| iv
1 | Introduction
| 1
2 | Elaboration of chosen principle to technical design
| 6
2.1 | Overview of technical design.
| 6
2.2 | Elaboration of technical design
| 6
2.2.1 | Mechanical
| 6
2.2.2 | Electrical
| 8
2.2.3 | Electronic
| 9
2.2.4 | Software
| 10
2.3 | Technical design integration
| 10

Functional Design | version no: | iv

## I. List of figures

Figure 1 Project management | Error! Bookmark not defined.
Figure 2 XKCD graph: walking back to my front door at night | Error! Bookmark not defined.

Functional Design | version no: | 1

## 1 Introduction

This document is a Technical Design Document for use by Ace Cars Projects. It provides guidance which is intended to assist the relevant management and technical staff, whether client or supplier, in producing a project‑specific Technical Design Document. It is also useful background reading for anyone involved in developing or monitoring the Ace car project.

Problem:

Developing a self-driving car using the ISH010 as a platform, the car can be left on a track and guide itself through it, evading obstacles, driving over a hill and stopping at the end of the track.

Background:

We were proposed to design a concept that would achieve automatization by our stakeholder, Saxion University of Applied Sciences, as a developing project to increase our skills and knowledge in this field.

Goals:

1. The drive is completely autonomous.
2. Evasion of obstacles in track.
3. Completement of the trial track.
4. Stop at the desired target.

Non-Goals

1. Develop our own platform system. Reason: we will be provided an already existing platform which we can modify.


Option 1:

Front wheel driven with a microcontroller as a processing platform, 1 optical sensor, 1 rotating DC motor type, capacitors, and batteries as energy storage, and with a sports car design.

This car will have great overall mechanical performance but may be compromised by the automation procedure.

Pros

- The pros of a FWD vehicle are that they are more energetically efficient. A FWD vehicle can maintain better traction since the weight of the engine is located over the driving wheels.
- The pros of using a microcontroller are the low time requirements for performing the operation. It is easy to use and troubleshooting and system maintenance are simple. At the same time, many tasks can be performed, so the human effect can be saved. The processor chip is exceedingly small, and flexibility occurs.
- The pros of using optic sensors are that they sense all kinds of materials, have a long life, have the longest sensing range, and have an extremely fast response time.
- The benefits of using capacitors and batteries as storage are that you will have a steady energy supply as well as fast bursts of energy from the capacitors when needed.
•

Cons

- The cons of FWS are that, since all the weight is in the front of the vehicle, front-wheel drive cars tend to understeer. During sudden acceleration, front-wheel-drive vehicles tend to veer to the right or left because of something called "torque steer." Front-wheel drive has worse acceleration than rear-wheel drive.
- The microcontroller cannot interface with high-power devices directly. It has a more complex structure as compared to the microprocessor. It only performs a limited number of executions simultaneously. It is used in micro-equipment.
- In optic sensors, the sensing range is affected by contamination by colour and reflectivity of the target, which might be a problem, especially for obstacle detection.

Option 2:

Front wheel driven with a microcontroller as a processing platform, 3 optical and acoustic sensors, 1 rotating AC motor type, a battery as a type of storage, and a convertible design.

This car will have great overall mechanical performance and automation performance. Even though it could lack of electrical capability.

Pros

- The pros of a FWD vehicle are that they are more energetically efficient. A FWD vehicle can maintain better traction since the weight of the engine is located over the driving wheels.
- The pros of using a microcontroller are the low time requirements for performing the operation. It is easy to use and troubleshooting and system maintenance are simple. At the same time, many tasks can be performed, so the human effect can be saved. The processor chip is ridiculously small, and flexibility occurs.
- The pros of using optic sensors are that they sense all kinds of materials, have a long life, have the longest sensing range, have an extremely fast response time, and by using an optic sensor, the system will be able to sense all materials.
- The pro of using batteries as storage is that you will enjoy the benefits of a steady energy supply and enormous amounts of it.
•

Cons

- The cons of FWD are that, since all the weight is in the front of the vehicle, front-wheel drive cars tend to understeer. During sudden acceleration, front-wheel-drive vehicles tend to veer to the right or left because of something called "torque steer." Front-wheel drive has worse acceleration than rear-wheel drive.
- The microcontroller can not interface with high-power devices directly. It has a more complex structure as compared to the microprocessor. It can only perform a limited number of executions simultaneously. It is used in micro-equipment.
- In optic sensors, the sensing range is affected by the colour and reflectivity of the target, which might be a problem, especially for obstacle detection. In acoustic sensors, the resolution of the frequency is a problem, as is the repeatability, and they are sensitive to temperature changes.

Option 3:

Rear wheel driven with a microcontroller as a processing system, 1 optical sensor, 1 rotating DC motor type, a battery as a type of storage, and a coupe design.

This car will have great overall mechanical performance but may be compromised by the automation procedure.

Pros

- Allowing the front tires to specialize in steering while the rear tires do the driving vastly improves both steering feel and ultimate cornering grip (mid-or rear-engine): Engine weight over drive wheels, plus dynamic rearward weight shift during acceleration, optimizes accelerative traction.
- The pros of using a microcontroller are the low time requirements for performing the operation. It is easy to use and troubleshooting and system maintenance are simple. At the same time, many tasks can be performed, so the human effect can be saved. The processor chip is exceedingly small, and flexibility occurs.
- The pros of using optic sensors are that they sense all kinds of materials, have a long life, have the longest sensing range, and have an extremely fast response time.
- The pros of using batteries as storage is that you will enjoy the benefits of a steady energy supply and large amounts of it.

Cons

- The cons of FWD are that the weight of the rear-wheel vehicle is much greater than that of a front-wheel vehicle. Because the engine is packaged outside the wheelbase and opposite the steering wheels, there may be reduced steering ability when the car accelerates. RWD has a slight loss in the efficiency of the drivetrain. The efficiency losses depend on the vehicle transmission.
- The microcontroller can not interface with high-power devices directly. It has a more complex structure as compared to the microprocessor. It only performs a limited number of executions simultaneously. It is used in micro-equipment.
- In optic sensors, the sensing range is affected by contamination by colour and reflectivity of the target, which might be a problem, especially for obstacle detection.

Option 4:

4x4 wheel driven with a PC as the processing system, 2 IR sensors, 2 rotating AC motor types, a battery as a type of storage, and a pickup design.

This option will provide good mechanical and drive performance but will lack weight and efficiency as the number of electrical components is high, draining a large part of the energy. It will also have very poor self-driving as the system is quite complex and has sensors that will not suit the job.

Pros

- Allowing the front tires to specialize in steering while the rear tires do the driving vastly improves both steering feel and ultimate cornering grip (mid-or rear-engine): Engine weight over drive wheels, plus dynamic rearward weight shift during acceleration, optimizes accelerative traction.
- The pros of using infrared sensors It gives assurance about correspondence because of the view or highlight point method of correspondence. The batteries utilized in infrared gadgets keep going for a long time because of their lower power utilization. Infrared movement sensors identify movement in the daytime and evening dependably. Infrared gadgets can quantify the distance to delicate items that may not be effortlessly identified by ultrasound.
- The pros of using batteries as storage is that you will enjoy the benefits of a steady energy supply and large amounts of it.

Cons

- The main disadvantage of 4WD is the added cost of purchase, maintenance, and energy. The extra equipment (differentials, transfer case, etc.) adds complexity and weight to the vehicle, increasing its initial market value, tire wear, and the cost of repairs and maintenance.
- *Infrared frequencies are influenced by hard objects (for example, dividers, entryways), smoke, dust, haze, daylight, and so on. Thus, it doesn’t work through dividers or entryways. Infrared waves of high force can harm the eyes. It underpins its more limited reach and, consequently, its execution corrupts longer distances.

Pros and cons motor types.

The most obvious difference is the type of current each motor turns into energy: alternating current in the case of AC motors, and direct current in the case of DC motors. AC motors are known for their increased power output and efficiency, while DC motors are prized for their speed control and output range.

Conclusion:

Our options provide very good overall performances. Thinking of efficiency, we could save some energy by modifying our current platform, which is an AWD chassis, to an FWD, making the power consumption less and having considerable powertrain performance. Even though this could make the steering of the cars less efficient and precise,

## 2 Elaboration of chosen principle to technical design

2.1 Overview of technical design.

To develop this project, we must look at the technical design. We must look at some of the systems features, such as mechanical, electronics, electrical, and software design, in a more detailed way. The purpose of a technical design document is to aid in the critical analysis of a problem and its proposed solution while also communicating priority, effort, and impact with stakeholders. A technical description describes a process in terms of its purpose, design, parts, and other key details.

We must start by analysing the specifications of the components' power consumption or the functions we could write in our code that will run in our system. Variables such as mass, forces, and velocities must be considered along with the way we are going to test them. It is incumbent upon us to make these calculations and analyse the ways to achieve the functional requirements from the technical part.

However, there is a big possibility that something will change in the technical part of our project because of innovative ideas or even better ideas to implement, and the team is willing to take a risk to make the job as best as possible.

2.2 Elaboration of technical design

For the elaboration of technical design, they split the workload into various parts and levels to better understand what must be done.

The main parts of elaboration are:

- Introduction
- Overview of technical design
- Mechanical part
- Electrical part
- Electronical part
- Software part
- Technical design integration.

Every section is detailed, described, and done with careful research into all the problems encountered by the team. Project activities take place after the detailed design but before the construction contract is tendered. The technical design stage develops the design in sufficient detail for co-ordination to be completed and enables packaged production information to be prepared, which can be passed to the contractor and their supply chain to construct the development.

2.2.1 Mechanical


Free body diagram [1]:

Base frame: ISH‑010

Transmission and power design


2.2.2 Electrical


Battery: Li-ion 2s 1p 7.4v 1500mAh

Discharge safety: 20% (The percentage left that is considered “fully discharged” to protect the battery from over discharge may be possible to go a bit lower but a lithium-ion (Li-ion) battery cannot be discharged below 2.5 volts and a lithium polymer (Li-Po) battery cannot be discharged below 3 volts, or battery damage will occur!).

Without Risking over-discharge, we could draw 2.5A continuously to get 30 minutes of power (if discharging 80% of the battery’s capacity)

Voltage conversions:

- Battery charger ->7.4v Li-Po
- 7.4v Li-ion -> Step-down converter (5v, 3.3v, …)
- 7.4v Li-ion-> Motor driver-> Motor(s)
- Step-down converter 5v-> Raspberry Pi, servo motor, Arduino, Camera, sensors…
- Step-down converter 3.3v-> Sensors

2.2.3 Electronic

ACE car decided to choose a Raspberry Pi microcomputer to communicate with a PC. The Raspberry Pi will transmit video data using either a camera connected directly to the raspberry pi’s camera port or a USB camera. It will send the video data to the PC, where it will then use OpenCV to process the frames and detect the track, obstacles, and hills. The PC will then send back control data to the Raspberry Pi, i.e., speed, steering, direction. ACE car has figured out a way to transmit smooth video through the network without much latency. As a result, our team is ready to move onto the next step.

Schematics:


Board Layout:


2.2.4 Software

- Machine Learning algorithms, Neural Networks Architecture.
Machine Learning allow a car to collect data from cameras and other sensors, interpret it, and decide what actions to take. Machine learning even allows cars to learn how to perform these tasks as good as humans or even better.
- Servo turning algorithm, Initialization of servo, DC motor, batteries etc.
- Appendix B.
Low level flow chart.
- Appendix A.
Software block diagram.
- Appendix C.
Architecture Overview
- C++, Python.
Python library allows to retrieve up to 90 FPS.
- Arduino IDE, Visual Studio Code, CLion IDE, ROS.
- Minimum required 3.20(CLion).

2.3 Technical design integration

Safety:

- The most dangerous part of the car is the battery. If a lithium-based battery experiences damage, it could potentially lead to a serious fire or explosion hazard.

Speed:

- AceCar’s current goal is to complete the track in under 1 min.

Accuracy:

- The car should measure the distance from the obstacle and find a way to avoid it. Typically, an ultrasonic sensor will be a good fit for this problem (other options exist).
- The car should be able to follow the white line without swinging side to side too much, or it will reduce the speed.

Cost:

- With the provided parts, the goal of an autonomous self-driving car simply cannot be achieved. Therefore, extra parts will be required. Depending on the parts used, the price will vary greatly.
- The base budget is around 50 euros, but if provided with satisfactory arguments, the budget limitation may be lifted.

Maintenance:

- The provided motor is a "brushed" DC motor, meaning as time goes on, the carbon "brushes" will wear out and will typically require replacing the whole motor or replacing the brushes if the motor has such capability.
- The battery is considered a consumable and will lose its capacity bit by bit, until one day it will require replacing.
- Gears: It is possible for the gears to break or wear out, thus requiring replacements.

## Appendix A: Software high level flow chart:


## Appendix B: Software Block Diagramm [2]:


## Appendix C: Architecture overview:

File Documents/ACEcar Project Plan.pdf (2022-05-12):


# Project plan


# Project: Autonomous Race car

# Company: ACEcar

Place, date: Enschede, 12th February 2022

Drawn up by: Jurijs Zuravlovs
| Dmytro Taras Karolis Juozapaitis Tarik Mandic Miguel Pérez Hernández
Version: | 1.1


Place, date: | Enschede, 12.02.2022
Prepared by: | ACEcar


| Miguel Pérez Hernández | 524262 | 524262@student.saxion.nl
| Tarik Mandic | 523830 | 523830@student.saxion.nl
| Karolis Juozapaitis | 517546 | 517546@student.saxion.nl
| Dmytro Taras | 516824 | 516834@student.saxion.nl
| Jurijs Zuravlovs | 440882 | 440882@student.saxion.nl
Version number: | [1.1]
Clients: | A. Yuksel, A. Fiselier, Y. Kasemsinsup

## Table of Contents

Table of Contents | 3
I | Abbreviations | 4
1 | Introduction | 1
1.2 Description | 1
1.3 MoSCoW Method | 2
2 | Project Objectives | 3
3 | Project Activities | 4
4 | Project Boundaries (scope and pre-conditions) | 6
5 | Results | 7
6 | Quality assurance | 9
7 | Project organization | 10
7.1 | Organisation | 10
7.2 | Information | 10
8 | Planning | 11
9 | Costs and benefits | 12
10 | Risk analysis | 13
Some members could be slacking off | 13
Not enough manpower or time to fulfil all the client’s expectations | 13
A mistake in the hardware or software | 13
Failure of Components | 13
Poor management | 13
Poor productivity | 13
Technical risks | 14
Bad timing | 14
Bibliography | Error! Bookmark not defined.
Appendix A | Gantt chart | 17
Appendix B | Risk analysis | 18


## I. Abbreviations

CV | Computer Vision
PCB | Printed Circuit Board
3D | 3 Dimensional


1 Introduction
ACEcar has been tasked with creating the best autonomous race car. Our team believes in the best quality, service, and smartest solution to a problem. Our crew is creating the high-end product. Our management team takes care of the best service and the smartest solutions for any given problem, and our support and developer teams make all dreams come true and create the best product. This project is very important to us because our team believes that every single task makes us better and all experience is good. To succeed in the current project, our team has conversations with clients to understand what is most important and uses the MoSCoW method to get the best ideas and solutions to archive our client's needs, as well as using the V model method to make our obstacles easier to archive and manage the workload.

1.2 Description
Our team has managed to come up with a simple solution for our brand's autonomous car. The circuit of this project contains hardware such as a processor. The processor controls the entire process—all units in the car, such as various sensors, motors, and lights. Sensor one indicates when the car can safely and autonomously drive at high speed along the given line, Sensor two indicates when the car encounters obstacles and drives around them, Sensor three looks to bring the car back to the line after encountering obstacles, and Sensor four indicates when there are no more lines, and the car simply stops at the finish line or end of the road. The first motor takes the car from steering, and the second motor accelerates the whole car. Light one indicates when the car is ready to operate, light two indicates when the battery has a low level of charge, and light three indicates when something is wrong, and the car is not ready. Race car have unique 3D printed model, which is super light and keep the car looking good and aerodynamic.

1.3 MoSCoW Method.
The MoSCoW method operates by splitting the clients’ requirements into the most important ("Must"), all the way down to additions which would be nice to have, but are not necessary ("Could"), while also agreeing on things which are not feasible due to either timing issues or just not enough manpower ("Won’t have").

Must:

- Follow the track line.
- Drive autonomously.
- Find the track line by itself.
- Stop at the end of the track
- Avoid any obstacles.

Should:

- Fit in a box of 400mm x 250mm x 200mm
- Drive for at least 30 minutes continuously
- have a body (3D printed separate parts)

Could:

- Accelerate to the maximum speed.
- Automatic return to start for charging or restarting mission
- Have a drone that follows the car autonomously to either give visual track data or to just record the car driving
- Make the car faster with either better or multiple motors
- Process the car through the network.
- Have a light that indicates whether they oversee the vehicle.
- Manual control through either a physical remote or laptop/phone/tablet

Won’t have:

- Solar powered batteries (which would contribute to sustainability and the renewable energy movement)
- More than two engines or batteries.
- An overkill engine
- Off road tires.

## 2 Project Objectives

The result of the project will be the design and realisation of an autonomous electrical racing car. The requirements that the car must follow are:

1. Ride autonomously.
2. Work for at least 30 minutes.
3. fit in a box of 400mm x 250mm x 200mm.
4. Follow the track line (20mm).
5. Stop at the end of the track.
6. Avoid obstacles.
7. Find the track line.
8. have a body (3D printed separate parts).

## 3 Project Activities

Project setup

1. Project plan.
2. User requirements.
3. Acceptance test plan.

System Requirements

1. Functional requirements.
2. Technical requirements.
3. System test plan.

Functional Design (High level design)

1. Concepts.
2. Choosing a concept.
3. Functional design concept chosen.
4. Sub-system test plan.

Technical design (Detailed design)

1. Technical block diagram.
2. Calculating and selecting essential components.
3. 3D and 2D mechanical design.
4. Schematics and PCB design.
5. Pseudo code.
6. Module/Unit test plan.

Realisation

1. Mechanical – Making components and module assembling.
2. Electrical-Electronic – Making PCBs and module assembling.
3. Software – module/unit coding.

Module/Unit Test

Sub-system Test

1. Module integration.
2. Test.

Factory Acceptance Test

1. Sub-system integration.
2. System Test.

Site acceptance Test

Finalization project

1. Final report & Documentation.
2. Personal contribution document.
3. PowerPoint presentation.

## 4 Project Boundaries (scope and pre-conditions)

Start day: 11th of February 2022

End day: 26th of May 2022

Length of the project: 105 days

Budget: 50€ (Unless “ACEcar” convinces the stake holders to increase the budget)

The pre-conditions that must be met for the project to have a chance of success:

- Project members each need to be assigned a role that the members will be working on (design, programming, management, electronics, etc.)
- “ACEcar” needs to decide on what technical approach will be chosen
- The preliminary design of the vehicle needs to be thought out for the prototype
- A prototype of the product needs to be made for testing purposes
- All important documents must be filled in and submitted
- The parts list must include the required parts price and links to the parts

What doesn’t belong in this project:

- A website promoting our company and product
- personnel other than the ACEcar team working on the project.

Project Schedule/Timetable:


## 5 Results

After the phases and activities are fulfilled, see chapter 3. These below will be the intermediate results for the project.

Project setup

- Project plan.

System Requirements

- A document containing the Functional and Technical requirements with the corresponding System Test plan.

Functional Design (High level design)

- A document containing different initial concepts and the final concept with the corresponding Sub-system test plan

Technical design (Detailed design)

- A document containing the technical design for mechanical, electrical/electronic and software with the corresponding module/unit test plan.

Realisation

- A document containing all the information and progress on the realisation on the mechanical – Making components and module assembling. Electrical-Electronic – Making PCBs and module assembling. Software – module/unit coding.

Module/Unit Test

- Documentation on the results of the individual parts which are the combined from the mechanical/ Electrical-Electronic/Software parts.

Sub-system Test

- Documentation on how and what was integrated into multiple modules and the Integration test results.

Factory Acceptance Test

- Documentation on how the different modules were integrated in one whole system and the System test results.

Site acceptance Test

- Documentation on the comparison of the end product, the system requirements and User requirements with the conclusion.

Finalization project

- Creation and handing in of the final report & documentation, personal contribution document and PowerPoint presentation.

## 6 Quality assurance

The desired quality will follow the project objectives mentioned in chapter 2:

1. Ride autonomously.
2. Work for at least 30 minutes.
3. fit in a box of 400mm x 250mm x 200mm.
4. Follow the white line (20mm).
5. Stop at the end of the track.
6. Avoiding obstacles.
7. Finding the white line.
8. have a body (3D printed separate parts).

The sponsor will assess the quality by testing the product on a track of a white line. That way 5 of the 8 objectives for the quality of the product will be assessed. The 2nd one will be done by riding in on a treadmill with a white line, the 3rd objective will be tested by measuring tape. And the 8th objective will be tested by sight and/or touch.

Before the production of the product, an order list, project plan, a functional and technical design must be created and submitted for feedback. Either to improve or change the conceptualization of the product.

The quality of the product will be tested by phase tests known as, Module/Unit Test, Sub-system Test, Factory Acceptance Test and Site acceptance Test.

External advice might be requested from other parties or experts to evaluate the intermediate product/results.

Some tools that might be used are:

- CLion.
- Visual studio code.
- Arduino IDE.
- Draw.io.
- Multisim/Uliboard/Altium.
- TinkerCad.
- SOLIDWORKS.
- Word.
- Teams.
- Excel.
- OpenCV + extra modules

## 7 Project organization

### 7.1 Organisation

Chief Financial Officer | Test engineer | Jurijs Zuravlovs | 440882 | +31647617551
Chief Information Officer | Software engineer | Dmytro Taras | 516824 | +31627251241
Chief Operating Officer | Mechanical engineer | Miguel Pérez Hernández | 524262 | +34620561978
Chief Executive Officer | Electrical engineer | Tarik Mandic | 523830 | +31639759355
Chief Technology Officer | Electronics engineer | Karolis Juozapaitis | 517546 | +31612636101

Test engineer - responsible for the testing part. Finding bugs and fixing them, Software, and hardware implementation testing
Software engineer - responsible for the software part of the project prototype and testing. Mechanical engineer - responsible for testing and mechanical part of the project
Electrical engineer - responsible for the hardware part of the project prototype and testing. Electronical engineer - hardware part of the project. Implementation testing and software

### 7.2 Information

Andre Fiselier, Ali Yuksel, Yanin Kasemsinsup are the stakeholders for this project. Communication with the stakeholders presented via meetings one time per week. During these meetings stakeholders can be reached to solve any issues and feedback on a project. The group itself also meets at this time but the group also can include meetings according to project model (SCRUM for example). For the stakeholder around 3 hours per week is defined while for the team meetings more hours expected. Project leader must handle reports to a stakeholder if it asked so. All the reports and working templates can be found on a cloud drive.

## 8 Planning


## 9 Costs and benefits

Project costs:

− Man-hours, 140 hours per person.

Project benefits:

− Reflect on the specific Body of Knowledge and Skills of ACS and EEE
− Understand the Arduino and several Shields and Modules for data processing and control − Do calculations, simulations and designing circuits for this Project
− Do electrical and mechanical measurements and software coding
− Do electrical and mechanical test measurement
− Implementing several electronic modules
− Building autonomous driving electrical Racing Car
− Work in a structured way to become a solution for a defined problem
− Experience Teamwork with individual responsibilities and work in a structured way − Organize a scheduled group and supervisor meeting
− Report technical information with specific software tools
− Do an Oral presentation with PowerPoint for a select Audience
− Perform respectively as a chairman and as a secretary in the group meetings
− Convince the Graders of your individual knowledge and skills improvement (reflection)

## 10 Risk analysis Conclusion

After gathering all the information, our team scored a pretty good score in risk analysis, meaning we can successfully continue our work. There are also many more risks that we take care of, and our management team analyses all of them to try to better succeed. To summarize, all risk assessment methods are considered the foundation for all operational risk assessment methods. Our strength of effectiveness is based on our teams' simplicity and ease of use, acting as quickly as possible on the numerous risks that need to be assessed.

Some members could be slacking off.
Split the work evenly and democratically. group meetings to learn about problems and solve them together. If some team members refuse to work together or refuse to participate in any type of work, the team has no choice but to vote them out of the team and project.

Not enough manpower or time to fulfil all the client’s expectations.
In order to ensure that all the client’s expectations are met, it is important to thoroughly plan out the workload between group members - if something seems too taxing to be implemented then the client is alerted beforehand, so as not to deliver a subpar product.

A mistake in the hardware or software.
By having everyone from the group check both the software and hardware portions of the project, we can ensure a high standard of value is upheld. Although this would take some more time, it ensures that everything the group does is done correctly, and as Linus’s law dictates: “given enough eyeballs, all bugs are shallow (Raymond and Torvalds, n.d.)”.

Failure of Components.
To avoid future errors in the system or mis failure of components, we would like to have some extra pairs of sensors, wires, LEDs, and parts to guarantee the quality of our product.

Poor management.
A project's success is dependent on good management. A good leader is supposed to have good communication and interaction with the team. Therefore, high standards are always set for the project manager.

Poor productivity.
To avoid low productivity among team members, the team leader should exercise strict control. In addition, there could also be a spread of the workload between the other members to avoid this risk.

Technical risks.
There may be a technical issue like a device that is not working, and this will be a risk as one of the members is out of the project unofficially. A way to solve this problem is to borrow this member a device or he himself finds one.

Bad timing.
To avoid this software development risk, apply agile methodologies, ensure the maximum involvement of all team members in planning and estimating, receive feedback at all stages, starting from the earliest ones, and involve the owner or stakeholders.

## Bibliography

Grit, R. (2010). Project managment. Noordhoff Uitgevers.

## Appendix A Gantt chart


## Appendix B Risk analysis

Risk | Value | Factor | Weight | Total risk
1. Estimated duration of the project? | 0–3 months 0 3–6 months 4 - 6+ months | 0 1 2 | X4 | 0
2. Does the project have a definite deadline? | No Flexible Yes | 0 2 4 | x4 | 16
3. Is there sufficient time to complete the project within the set period? | more than enough enough not enough | 0 1 3 | x4 | 4

Complexity of the project
4. The number of functional subsectors involved? | 1 2 3+ | 0 1 3 | x4 | 12
5. The number of functional subsectors that will make use of the outcomes? | 1 2-3 4 | 0 1 2 | x2 | 4
6. Is it a new project or one that has been adapted? | minor adaptions major adaptions new project | 0 2 3 | x5 | 15
7. To what extent do the present authorisations have to be adjusted? | Not minor extent medium extent major extent | 0 1 2 3 | x5 | 5
8 Are other projects dependent on this one? | No yes, though the deadlines are not tight yes, and the deadlines are tight | 0 1 3 | x5 | 15
9. What sort of reception are the users likely to give it? | Enthusiastic noncommittal interested | 0 1 2 | x5 | 5
10. Has the project been divided up into phases and is progress dependent on the coordination between them? | No a little strongly | 1 2 3 | x3 | 15

Project group

11. Where do the project workers come from? | mainly internally partly internally mainly externally | 0 1 3 | x4 | 4
12. Where is the project located? | 1 location 1 to 3 locations more than 3 locations | 0 1 2 | x2 | 0
13. The number of projects taking up more than 80% of peak hours? | 1–5 5–10 5 – 10+ | 0 2 4 | x5 | 10
14. The balance between subject experts and project experts? | Good Average unfavourable | 0 2 4 | x5 | 0
15. Are the users involved in the project? | to a large extent to a reasonable extent to a limited extent | 0 1 3 | x3 | 9

The project management
16. Does the project management team have any knowledge of the subject? | a lot a reasonable amount little | 0 2 4 | x3 | 6
17. Does the project management have any knowledge of how to plan a project? | a lot a reasonable amount little | 0 2 4 | x3 | 6
18. How much experience does the project manager have with projects like this? | a lot a reasonable amount little | 0 1 3 | x3 | 3
19. Do the advisers have any knowledge of the field of research? | a lot a reasonable amount little | 0 1 3 | x5 | 0
20. Do the subject experts have much knowledge of the field? | a lot a reasonable amount little | 0 1 3 | x5 | 0
21. How involved in the project are the managers responsible for it? | Very | 0 | x5 | 10

| reasonably involved only slightly | 2 5
22. Is there any chance that the project team will change during the project? | little chance some chance big chance | 0 2 5 | x5 | 0
23. Is the project group using existing methods or creating its own methods? | only existing methods some existing methods no existing methods | 0 2 4 | x4 | 0

Project definition
24. Are the project members sufficiently aware of the problems and objectives? | yes, everybody most of them not all of them | 0 1 5 | x5 | 0
25. Is the field of research sufficiently demarcated? | yes reasonably not clearly | 0 2 5 | x5 | 10
26. Is there sufficient demarcation between this project and other projects? | considerable reasonable insufficient | 0 1 3 | x4 | 0
27. Has enough time been reserved for coordination and decision-making? | considerable reasonable insufficient | 0 1 3 | x4 | 0
28. Are the boundaries clearly demarcated? | Yes in general most of them are not | 0 1 3 | x4 | 0
29 Are the boundaries limiting enough? | Yes moderately no | 0 2 5 | x5 | 10

Risk percentage = total
max score

x100% = 35%

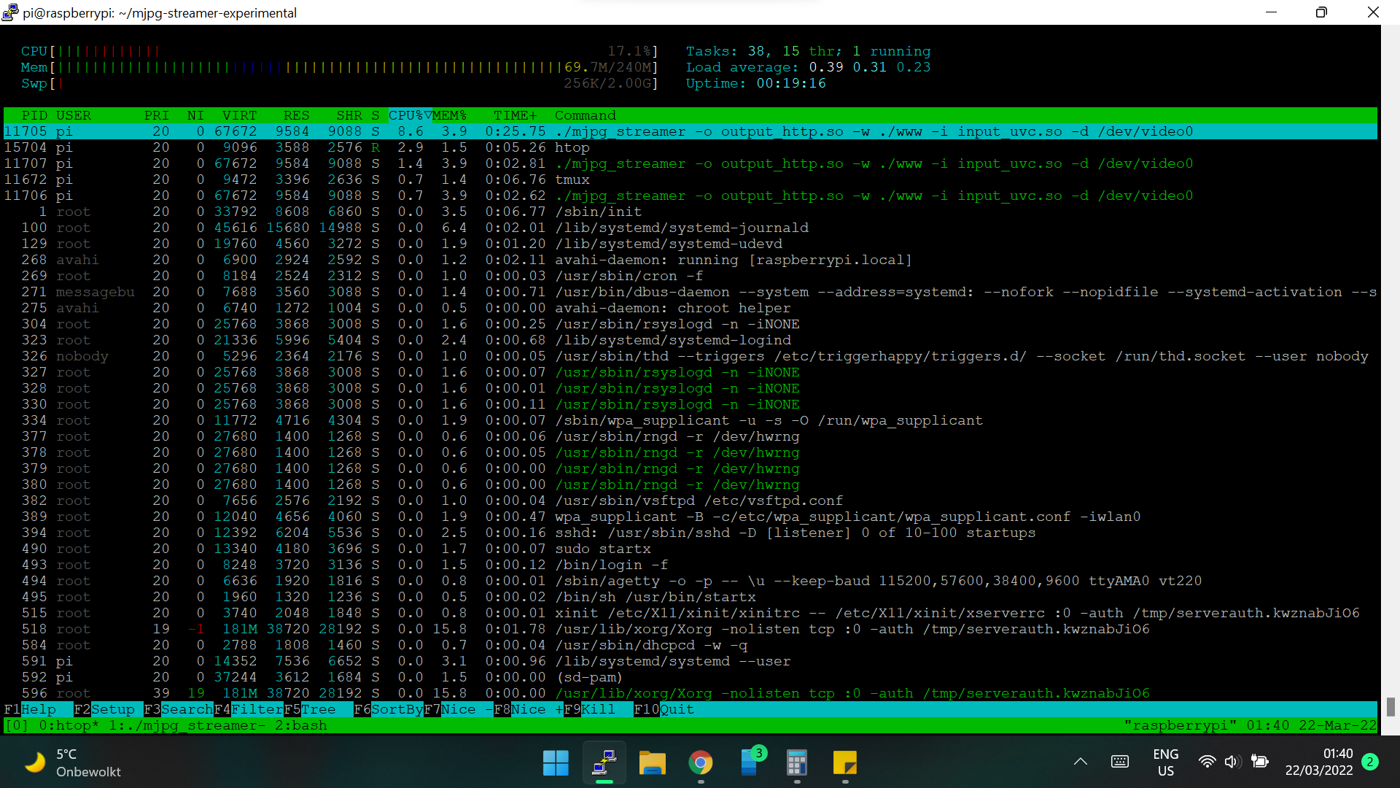
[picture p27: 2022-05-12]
Pictures and videos/Screenshot 2022-03-22 014057.png

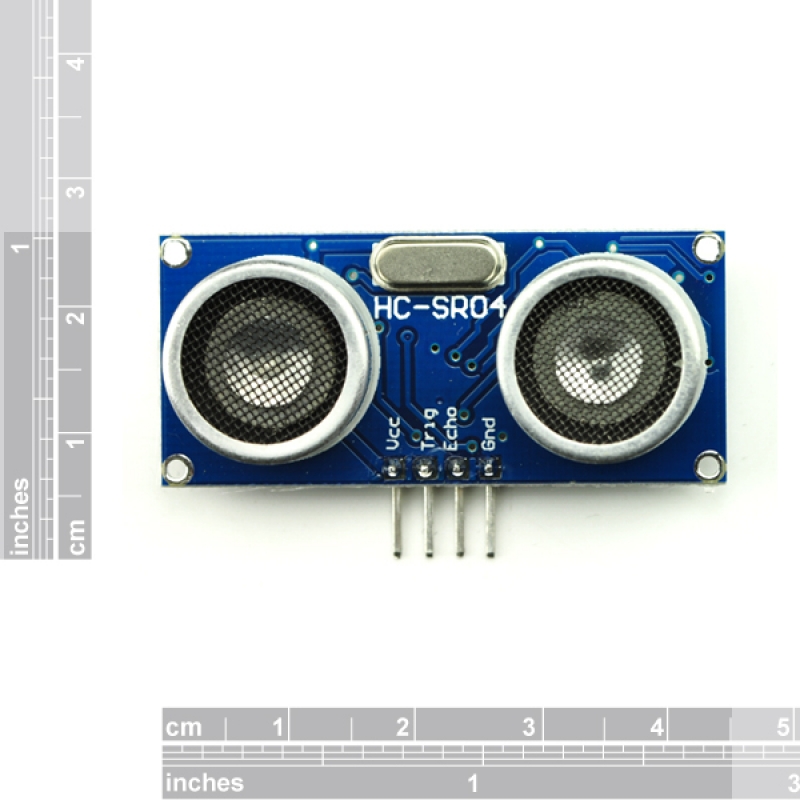
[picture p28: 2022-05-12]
Componet skteches/SR04-3-800x800.jpg

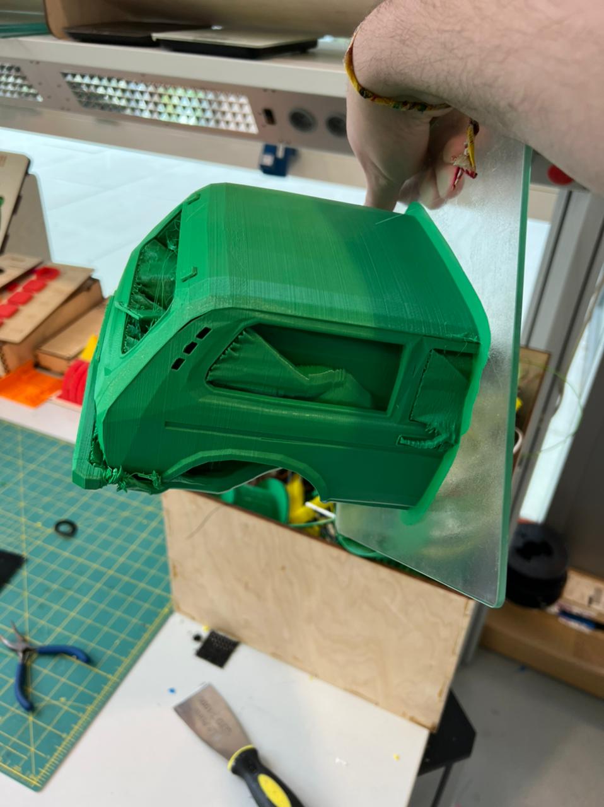
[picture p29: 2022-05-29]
Pictures and videos/9b47be92-8a3d-464e-97e3-66ebbd837ca1.jpg

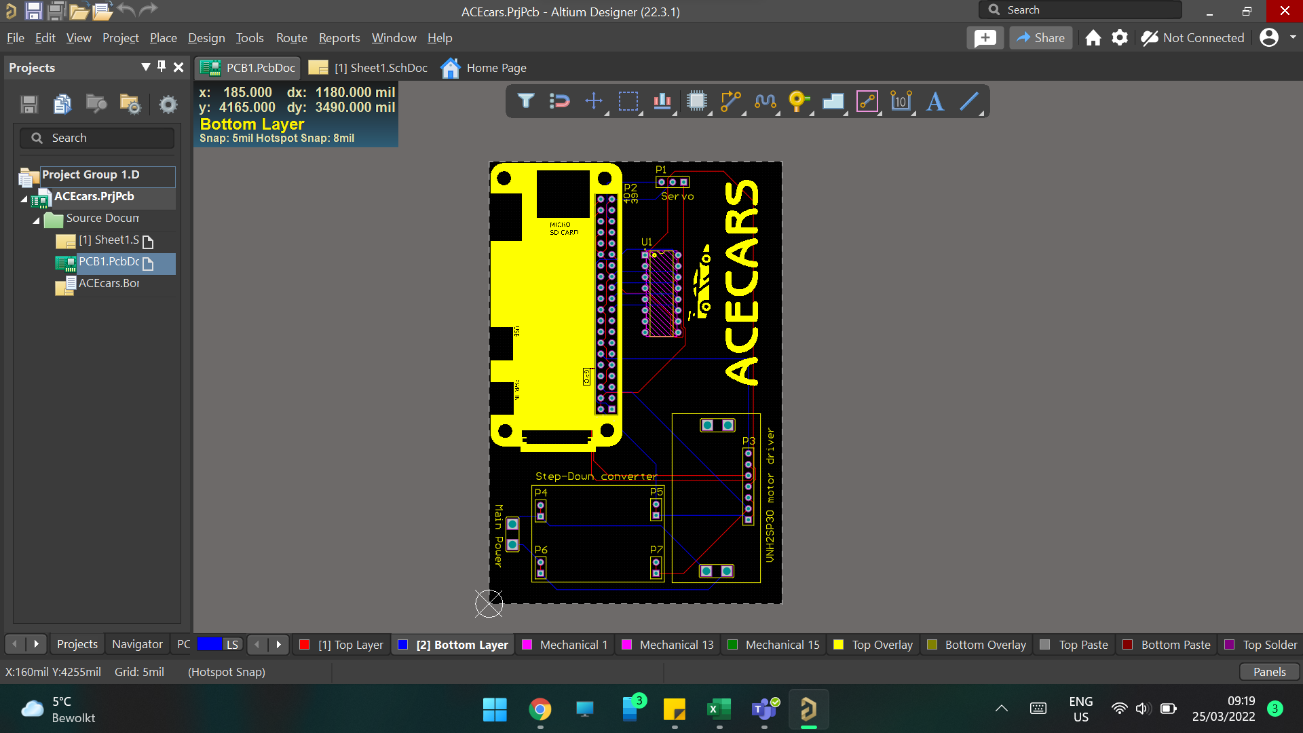
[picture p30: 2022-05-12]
Pictures and videos/Screenshot 2022-03-25 091916.png

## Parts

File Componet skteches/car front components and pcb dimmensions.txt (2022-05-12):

Front components:
	Camera:
		Dimmensions:
			x:24.92 mm
			y:24.21 mm
		Thickness:
			PCB:1.00 mm
			PCB + Connector:3.57 mm
			PCB + camera:5.85

	Ultrasonic sensor:
		dimmensions:
			x:45.50 mm
			y:20.41 mm
		Thickness:
			PCB:1.20 mm
			PCB + sensor:13.55 mm

	8X IR sensor:
		dimmensions:
			x:66.05 mm
			y:16.02 mm
		Thickness:
			PCB:1.80 mm
			PCB + sensor:3.23 mm

Main PCB:
	Dimmensions:
		x:92.583mm
		y:66.675mm
	Thickness:
		pcb:depends (might be 1.60 mm)
		everything: +-25mm (probably best to have atleast +5 mm clearance)

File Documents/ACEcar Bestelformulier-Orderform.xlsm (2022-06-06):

Bestelweb
Bestelformulier voor LED / LED Orderform
Dit formulier kan worden gebruikt voor het aanvragen (per mail) voor het plaatsen van een order in Bestelweb.
Alle opdrachten voor levering van goederen en diensten die resulteren in een factuur aan SAXION dienen in Bestelweb te worden geregistreerd. This orderform is used for requesting goods via mail.
Aanvraag
Naam/Name: |  | ACEcar Autonomous racing car
Datum/Date: |  | 2022-03-28
Budgethouder:
Kostenplaats: |  | 1150375
Kostensoort:
Prijzen zijn exclusieve BTW / Prizes are excl. VAT
Leverancier/ Vendor: |  | Saxion
Artikelen/Articles/diensten/Services:
Nr. | Artikelnr. | Omschrijving / Description | Aantal/Quantity | Prijs/stuk (€) Price/unit (€) | Totaal (€)
1 |  | DC-DC Step-down Buck Converter 5A - 5V output (https://www.tinytronics.nl/shop/nl/power/spanningsconverters/buck-(step-down)-converters/dc-dc-step-down-buck-converter-5a-5v-output) | 1.00 | 2.48 | 2.48
2 |  | Raspberry zero 2 w kit (https://www.kiwi-electronics.nl/nl/raspberry-pi-zero-2-w-basic-pack-10821?language=nl-nl&currency=EUR) | 1.00 | 30.54 | 30.54
3 |  | MCP3008 8-chan 10 bit SPI ADC (https://www.tinytronics.nl/shop/nl/componenten/ic's-en-microcontrollerchips/ic's/mcp3008-8-kanaals-10-bit-adc-chip-spi-16-pin-dip) | 2.00 | 2.48 | 4.96
4 |  | 8x IR Line Tracking Module (https://www.tinytronics.nl/shop/nl/sensoren/optisch/infrarood/8x-ir-lijn-tracking-module) | 1.00 | 3.72 | 3.72
5 |  | Raspberry Pi Zero Camera Cable - 15 pin FPC-FFC flex - 15cm (https://www.tinytronics.nl/shop/nl/kabels-en-connectoren/kabels-en-adapters/ffc/raspberry-pi-zero-camerakabel-15-pin-fpc-ffc-flex-15cm) | 1.00 | 2.48 | 2.48
6 |  | Raspberry Pi Compatible Camera 5MP V1.3 (https://www.tinytronics.nl/shop/nl/sensoren/optisch/camera's-en-scanners/raspberry-pi-compatible-camera-5mp-v1.3) | 1.00 | 6.61 | 6.61
7 |  | Ultrasonic Sensor - HC-SR04 (https://www.tinytronics.nl/shop/nl/sensoren/afstand/ultrasonische-sensor-hc-sr04) | 1.00 | 2.48 | 2.48
8
9
10
11
12
13
14
 |  |  |  | Totaal Excl. BTW: | 53.27
Kostenplaats | Naam

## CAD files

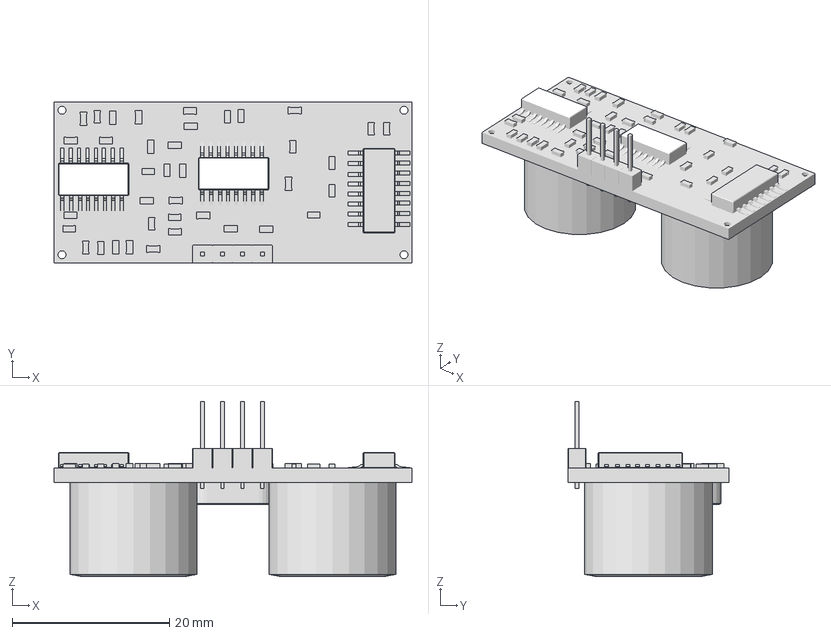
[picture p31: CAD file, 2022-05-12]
Componet skteches/Ultrasonic(FRONT for obstacles).3mf
45.5 x 20.4 x 22.3 mm

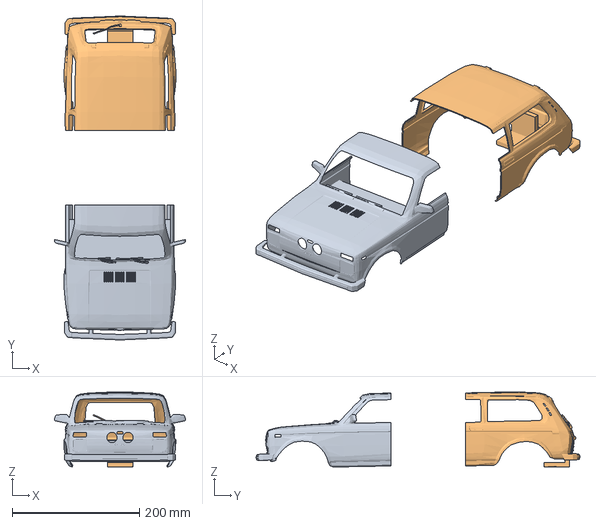
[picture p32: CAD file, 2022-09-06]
Documents/CAD Files/Split car.3mf
206.4 x 508.6 x 117.7 mm

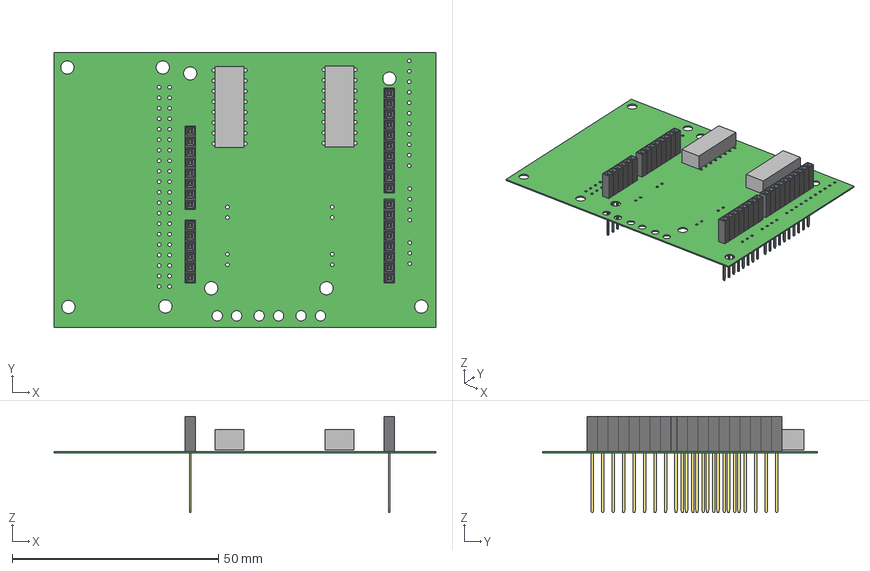
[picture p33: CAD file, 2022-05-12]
Componet skteches/PCB1.step
92.6 x 66.7 x 23.4 mm
Extruded x 2
SIL_Socket_Body x 32
SIL_SocketPin x 32

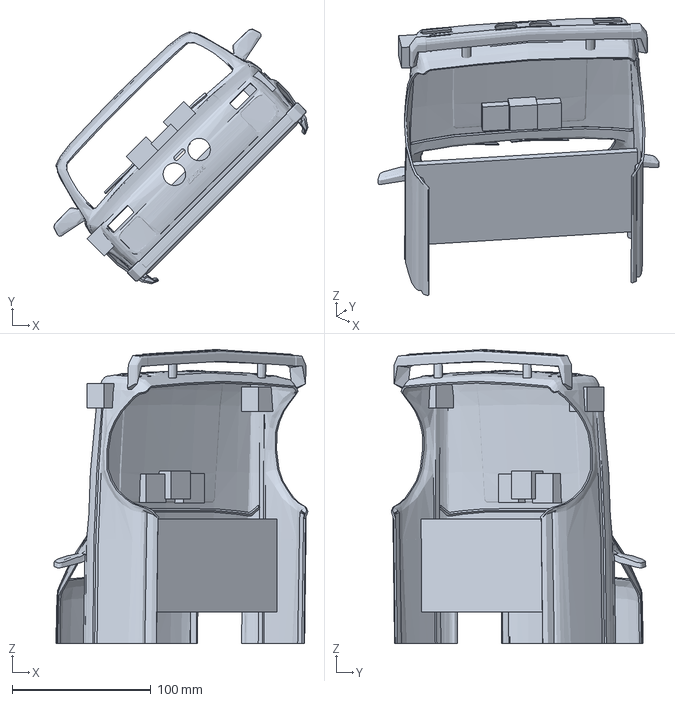
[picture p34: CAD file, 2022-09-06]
Documents/CAD Files/UM2E_Front car.3mf
183.2 x 183.7 x 212.2 mm

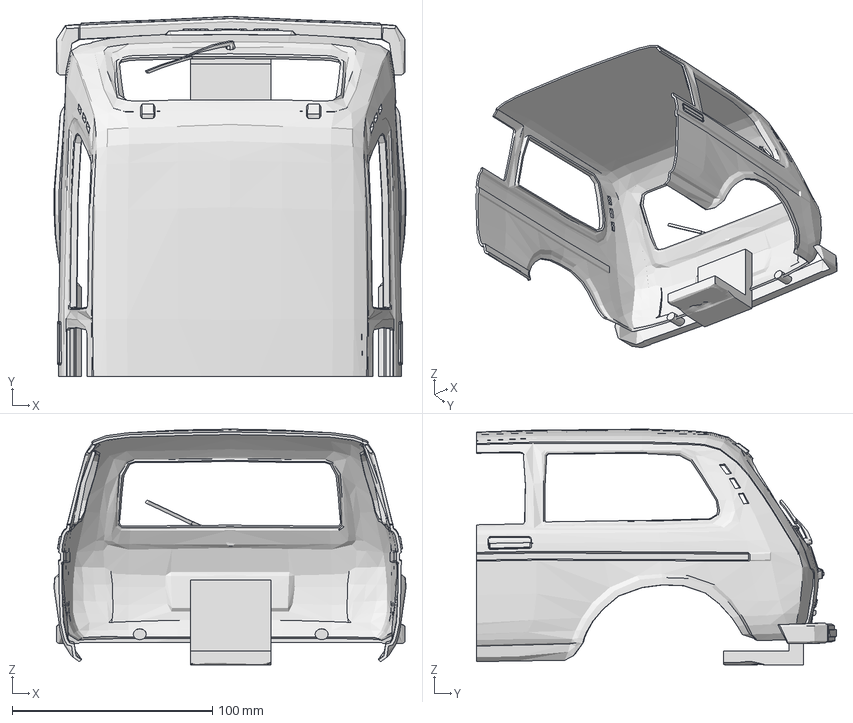
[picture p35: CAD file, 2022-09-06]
Documents/CAD Files/Back car.3mf
175.7 x 179.8 x 117.7 mm

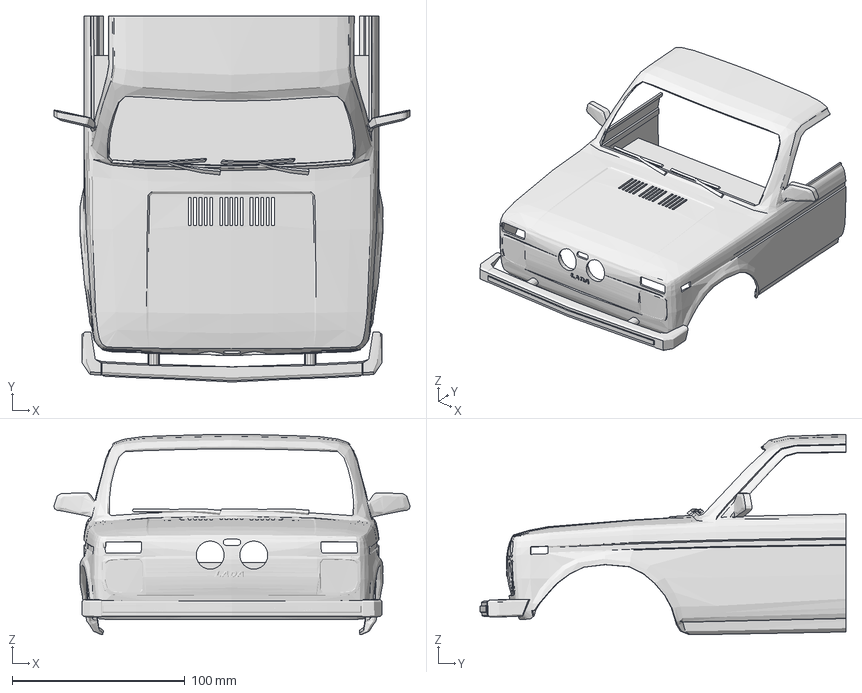
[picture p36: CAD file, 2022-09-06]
Documents/CAD Files/Front car.3mf
206.4 x 212.2 x 116.2 mm

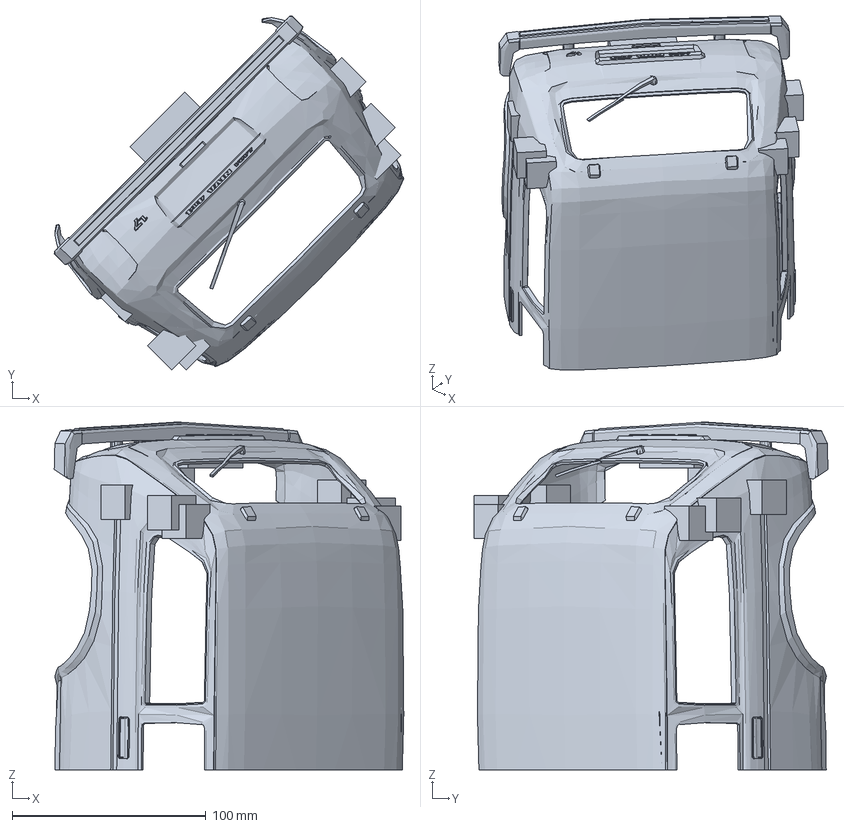
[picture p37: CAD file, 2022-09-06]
Documents/CAD Files/UM2E_Back car.3mf
180.6 x 182.9 x 179.8 mm

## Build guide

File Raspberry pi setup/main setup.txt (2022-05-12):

########SETUP#################

sudo apt-get update -y &&
sudo apt-get upgrade -y &&
sudo apt-get install -y git cmake

################install mjpeg-streamer#####################

sudo apt install libjpeg9-dev
git clone https://github.com/jacksonliam/mjpg-streamer.git
cd mjpg-streamer-experimental

MAKE CHANGES ON CONFIG USING THIS PULL REQUEST (as of 2022-05-12 pull request not merged)
https://github.com/jacksonliam/mjpg-streamer/pull/350/commits/8895ed4f825846fd27c468fbe2139bf69e09d684
make
sudo make install

mjpg_streamer -i "input_uvc.so" (to use usb camera)
mjpg_streamer -i "input_raspicam.so" (to use raspi camera)

##############Increase swap size######################################################################

sudo dphys-swapfile swapoff
sudo nano /etc/dphys-swapfile (change to CONF_SWAPSIZE=2048) 	
sudo dphys-swapfile setup
sudo dphys-swapfile swapon
sudo reboot

############clone into opencv files##############################

git clone https://github.com/opencv/opencv.git &&
git -C opencv checkout 4.x &&
git clone https://github.com/opencv/opencv_contrib.git &&
git -C opencv_contrib checkout 4.x &&
mkdir build &&
cd build

###############install essential packages######################################

sudo apt-get install -y build-essential pkg-config libgtk-3-dev \
    libavcodec-dev libavformat-dev libswscale-dev libv4l-dev \
    libxvidcore-dev libx264-dev libjpeg-dev libpng-dev libtiff-dev \
    gfortran openexr libatlas-base-dev python3-dev python3-numpy \
    libtbb2 libtbb-dev libdc1394-22-dev python3-pip

############install gstreamer packages########################################################

sudo apt-get install -y libgstreamer1.0-0 gstreamer1.0-plugins-base gstreamer1.0-plugins-good gstreamer1.0-plugins-bad gstreamer1.0-plugins-ugly gstreamer1.0-libav gstreamer1.0-tools gstreamer1.0-x gstreamer1.0-alsa gstreamer1.0-gl gstreamer1.0-gtk3 gstreamer1.0-pulseaudio
sudo apt-get install -y libgstreamer1.0-dev libgstreamer-plugins-base1.0-dev &&
sudo apt-get install -y gstreamer1.0-tools &&
sudo apt-get install -y libavcodec-dev libavformat-dev libavutil-dev libswscale-dev libavresample-dev &&
sudo apt-get install -y pkg-config &&
sudo apt-get install -y libgtk-3-dev &&
sudo apt-get install -y libgtk2.0-dev &&
sudo apt-get install -y libdc1394-dev

#########run cmake with gstreamer Python and contrib modules enabled###########################
(in build dir)

sudo cmake -D CMAKE_BUILD_TYPE=RELEASE \
-D WITH_GSTREAMER=ON \
-D OPENCV_GENERATE_PKGCONFIG=ON \ 
-D OPENCV_EXTRA_MODULES_PATH=~/ACEcar/opencv/opencv_contrib/modules ~/ACEcar/opencv/opencv

#####################compile################################

make -j4
sudo make install

###############Optional packaeges####################

sudo apt install tmux (recomended to run docked consoles)
sudo apt install cmake-gui

################xserver################################

sudo apt-get install xserver-xorg-core xserver-xorg-input-all \
xserver-xorg-video-fbdev libx11-6 x11-common \
x11-utils x11-xkb-utils x11-xserver-utils xterm lightdm openbox

###############ENABLE REMOTE GPIO##################################
sudo apt install pigpio
sudo raspi-config -> Interfaces -> Remote GPIO -> Yes
sudo systemctl enable pigpiod

https://abyz.me.uk/rpi/pigpio/python.html#pigpio.pi (More info)
https://gpiozero.readthedocs.io/en/stable/remote_gpio.html(More info)

####################SOURCES##################

https://linuxize.com/post/how-to-install-opencv-on-debian-10/

https://abyz.me.uk/rpi/pigpio/python.html#pigpio.pi (More info)
https://gpiozero.readthedocs.io/en/stable/remote_gpio.html(More info)

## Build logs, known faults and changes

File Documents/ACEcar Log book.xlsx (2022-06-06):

Logbook - project Race car |  |  |  |  | Name: Jurijs Z.(440882), Karolis J.(517546),Tarik M.(523830)
Company: ACEcar |  |  |  |  | Dmytro T.(516824), Miguel P.M.(524262) |  |  |  |  | Legenda
Legnda - A, B, J |  |  |  |  |  |  |  |  |  | Code | Location
The locations and corresponding code can be found in the legenda |  |  |  |  |  |  |  |  |  | A | Personal residence
 | Week | 1 |  |  |  |  |  |  | total time | B | W2.40 -Saxion
Work done | Date | 2022-02-07 | 2022-02-08 | 2022-02-09 | 2022-02-10 | 2022-02-11 | 2022-02-12 | 2022-02-13 | x | C | W2.29a - Saxion
Lecture |  | 0.45 |  |  |  | 3.15 |  |  | 3.6 | D | W2.30a - Saxion
Problem definition |  |  |  |  |  | 1 |  |  | 1 | E | W2.30b - Saxion
Project plan |  |  |  |  |  | 0.5 | 1 | 2 | 3.5 | F | OTSWO - Saxion
Quality |  |  |  |  |  |  |  | 1 | 1 | G | W3.47 - Saxion
Risk assesment |  |  |  |  |  |  | 1 |  | 1 | H | W2.42 - Saxion
General planning |  |  |  |  |  |  |  | 1 | 1 | I | W2.43 - Saxion
Personal planning |  |  |  |  |  | 1 |  |  | 1 | J | FabLab
Meeting |  |  |  |  |  | 0.5 |  |  | 0.5 | # hr | Hours spend
Prepare meeting |  |  |  |  |  | 0.5 |  |  | 0.5
 |  |  |  |  |  |  | Subtotal |  | 13.1
 | Week | 2 |  |  |  |  |  |  | total time
Work done | Date | 2022-02-14 | 2022-02-15 | 2022-02-16 | 2022-02-17 | 2022-02-18 | 2022-02-19 | 2022-02-20 | x
Meeting |  |  |  |  |  | 0.5 |  | 0.5 | 1
Project plan |  |  |  |  |  | 1 | 1 | 1 | 3
Risk assesment |  |  |  |  | 1 |  | 1 |  | 2
quality |  |  |  |  |  | 1 |  | 1 | 2
Lecture |  | 0.45 |  |  |  | 3.15 |  |  | 3.6
Logbook |  |  |  |  |  |  | 0.1 |  | 0.1
Prepare meeting |  |  | 1 |  |  | 1 |  |  | 2
 |  |  |  |  |  |  | Subtotal |  | 13.7
 |  |  |  |  |  |  | Accumulative total |  | 26.8
 | Week | 3 |  |  |  |  |  |  | total time
Work done | Date | 2022-02-28 | 2022-03-01 | 2022-03-02 | 2022-03-03 | 2022-03-04 | 2022-03-05 | 2022-03-06 | x
Functional design |  |  | 1 |  | 1 | 3 | 1 | 1 | 7
Measurement plan |  |  | 1 |  |  |  | 1 |  | 2
Measurement plan research |  |  | 1 |  |  |  |  | 3 | 4
 |  |  |  |  |  |  | subtotal |  | 13
 |  |  |  |  |  |  | accumulative total |  | 39.8
 | Week | 4 |  |  |  |  |  |  | total time
Work done | Date | 2022-03-07 | 2022-03-08 | 2022-03-09 | 2022-03-10 | 2022-03-11 | 2022-03-12 | 2022-03-13 | x
Lecture |  |  | 0.45 |  |  | 3.15 |  |  | 3.6
Prepare meeting |  |  |  |  |  |  | 0.5 |  | 0.5
Meeting |  |  |  |  |  |  | 1 |  | 1
Doing measurements |  |  |  |  |  | 1 |  |  | 1
Processing measurements |  |  |  |  |  |  | 0.5 |  | 0.5
Tests research |  |  |  |  | 1 |  |  | 2 | 3
Physical measurements machine |  |  |  |  | 1 |  | 1 |  | 2
Functional design plan |  |  |  |  | 1 |  |  | 1 | 2
Finalize functional design |  |  |  |  |  | 1 | 1 | 1 | 3
 |  |  |  |  |  |  | Subtotal |  | 16.6
 |  |  |  |  |  |  | Accumulative total |  | 56.4
 | Week | 5 |  |  |  |  |  |  | total time
Work done | Date | 2022-03-14 | 2022-03-15 | 2022-03-16 | 2022-03-17 | 2022-03-18 | 2022-03-19 | 2022-03-20 | x
Lecture |  |  | 0.45 |  |  | 3.15 |  |  | 3.6
Prepare meeting |  |  |  |  |  | 0.5 |  |  | 0.5
improve functional design |  |  | 1 |  |  |  |  |  | 1
Adapt functional design |  |  |  | 1 |  | 0.1 |  |  | 1.1
Go/No Go meeting |  |  |  |  |  | 0.1 |  |  | 0.1
Prepare Go/No go |  |  |  |  | 1 | 1 |  |  | 2
Technical design research |  |  |  |  | 1 |  | 1 | 1 | 3
Technical design discussion |  |  |  |  |  |  | 1 | 1 | 2
 |  |  |  |  |  |  | Subtotal |  | 13.3
 |  |  |  |  |  |  | accumulative total |  | 69.7
 | Week | 6 |  |  |  |  |  |  | total time
Work done | Date | 2022-03-21 | 2022-03-22 | 2022-03-23 | 2022-03-24 | 2022-03-25 | 2022-03-26 | 2022-03-27 | x
Lecture |  |  | 0.45 |  |  | 3.15 |  |  | 3.6
prepare meeting |  |  |  |  | 0.5 |  |  |  | 0.5
Mechanical design |  |  |  |  |  |  | 1 |  | 1
Set up TAR |  |  |  |  | 1 |  |  |  | 1
Meeting |  |  | 1 |  |  |  | 1 | 1 | 3
3D scan coffeemachine |  |  | 1 | 1 | 1 | 1 | 1 | 1 | 6
Finish TD |  |  | 1 |  |  | 1 | 1 | 1 | 4
 |  |  |  |  |  |  | Subtotal |  | 19.1
 |  |  |  |  |  |  | accumulative total |  | 88.8
 | Week | 7 |  |  |  |  |  |  | total time
Work done | Date | 2022-03-28 | 2022-03-29 | 2022-03-30 | 2022-03-31 | 2022-04-01 | 2022-04-02 | 2022-04-03 | x | Legenda
Prepare meeting |  |  |  |  |  | 0.5 |  |  | 0.5 | Code | Location
Meeting |  |  |  |  |  | 1 |  |  | 1 | A | Personal residence
Polish mechanical design |  |  |  |  | 1 | 1 |  |  | 2 | B | W2.40 -Saxion
Assist in PCB design |  |  |  |  | 1 |  | 1 | 1 | 3 | C | W2.29a - Saxion
Component selection |  |  | 1 |  |  | 1 |  |  | 2 | D | W2.30a - Saxion
Fablab preparation |  |  |  |  | 1 | 2 | 1 | 1 | 5 | E | W2.30b - Saxion
 |  |  |  |  |  |  |  |  | 0 | F | OTSWO - Saxion
 |  |  |  |  |  |  | Subtotal |  | 13.5 | G | W3.47 - Saxion
 |  |  |  |  |  |  | accumulative total |  | 102.3 | H | W2.42 - Saxion
 |  |  |  |  |  |  |  |  |  | I | W2.43 - Saxion
 |  |  |  |  |  |  |  |  |  | J | FabLab
 |  |  |  |  |  |  |  |  |  | # hr | Hours spend
 | Week | 8 |  |  |  |  |  |  | total time
Work done | Date | 2022-04-04 | 2022-04-05 | 2022-04-06 | 2022-04-07 | 2022-04-08 | 2022-04-09 | 2022-04-10 | x
Prepare meeting |  |  | 0.5 |  |  | 0.5 |  |  | 1
Meeting |  |  | 1 |  |  | 2 |  |  | 3
Prepare PCB print |  |  |  | 1 | 1 | 1 |  |  | 3
Prepare laser cutting |  |  |  |  | 1 |  |  |  | 1
Laser cutting |  |  | 1 |  |  |  | 1 |  | 2
Assist in pcb design |  |  |  |  |  | 1 |  |  | 1
 |  |  |  |  |  |  | Subtotal |  | 11
 |  |  |  |  |  |  | accumulative total |  | 113.3
 | Week | 9 |  |  |  |  |  |  | total time
Work done | Date | 2022-04-25 | 2022-04-26 | 2022-04-27 | 2022-04-28 | 2022-04-29 | 2022-04-30 | 2022-05-01 | x
Compose component list |  |  | 1 |  |  | 1 |  |  | 2
Case design tweaks |  |  |  |  |  | 1 |  |  | 1
PCB tweaks |  |  | 1 |  |  | 1 |  |  | 2
PCB Print preparation |  |  | 1 |  | 1 | 1 | 1 | 1 | 5
PCB Printing |  |  |  |  |  | 1 |  |  | 1
 |  |  |  |  |  |  | Subtotal |  | 11
 |  |  |  |  | 1 |  | accumulative total |  | 113.3
 | Week | 10 |  |  |  |  |  |  | total time
Work done | Date |  |  |  |  |  |  |  | x
Exam week
PCB printing |  |  |  |  |  |  |  |  | x
 |  |  |  |  |  |  | accumulative total
 |  |  |  |  |  |  |  |  |  | Legenda
 | Week | 11 |  |  |  |  |  |  | total time | Code | Location
Work done | Date |  |  |  |  | x |  |  | x | A | Personal residence
Exam week |  |  |  |  |  |  |  |  |  | B | W2.40 -Saxion
 |  |  |  |  |  |  |  |  |  | C | W2.29a - Saxion
 |  |  |  |  |  |  |  |  |  | D | W2.30a - Saxion
 |  |  |  |  |  |  |  |  |  | E | W2.30b - Saxion
 |  |  |  |  |  |  |  |  |  | F | OTSWO - Saxion
 | Week | 12 |  |  |  |  |  |  | total time | G | W3.47 - Saxion
Work done | Date |  |  |  |  |  |  |  | x | H | W2.42 - Saxion
Holiday |  |  |  |  |  |  |  |  |  | I | W2.43 - Saxion
 |  |  |  |  |  |  |  |  |  | J | FabLab
Prepare meeting |  |  |  |  |  |  |  | 1 | 1 | # hr | Hours spend
 |  |  |  |  |  |  | accumulative total |  | 1
 | week | 13 |  |  |  |  |  |  | total time
Work done | Date | 2022-05-09 | 2022-05-10 | 2022-05-11 | 2022-05-12 | 2022-05-13 | 2022-05-14 | 2022-05-15 | x
Meeting |  |  | 1 |  |  |  |  | 1 | 2
Assembly preparations |  | 1 | 1 |  |  |  |  |  | 2
Mechanical design revison |  | 2 | 1 |  |  |  |  |  | 3
Finalize report template |  | 2 |  |  |  |  |  | 1 | 3
Recutting Casing |  | 1 |  |  |  |  |  |  | 1
Soldering mega shield |  |  | 1 | 1 |  |  |  |  | 2
Prepare meeting |  | 0.5 | 1 |  |  |  |  |  | 1.5
 |  |  |  |  |  |  | Subtotal |  | 14.5
 |  |  |  |  |  |  | accumulative total |  | 128.8
 | week | 14 |  |  |  |  |  |  | total time
Work done | Date | 2022-05-23 | 2022-05-24 | 2022-05-25 | 2022-05-26 | 2022-05-27 | 2022-05-28 | 2022-05-29 | x
Meeting |  | 1 | 1 |  |  |  |  |  | 2
Lecture |  |  | 3 |  |  |  |  |  | 3
Performance testing |  | 2 | 1 |  |  |  |  |  | 3
Finalize report |  | 2 | 1 |  |  |  |  |  | 3
Regression testing |  | 2 | 1 |  |  |  |  |  | 3
Acceptance testing |  | 2 |  |  |  |  |  |  | 2
Main system report |  | 2 |  |  |  |  |  |  | 2
 |  |  |  |  |  |  | Subtotal |  | 18
 |  |  |  |  |  |  | accumulative total |  | 146.8

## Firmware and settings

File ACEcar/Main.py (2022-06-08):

##########IMPORTS##########
import cv2
import time
import pigpio
import keyboard
import threading
import numpy as np


########OUTPUT PINS########

ServoPin = 13
MotorPin = 12
INA = 5
INB = 6


########MIN/MAX VALUES########

# Line following threshold
CX_MIN = 200
CX_MAX = 300

# Obstacle avoidance threshold
OBY_MIN = 200
OBY_MAX = 300

# Min/Max obstacle stop values
STOP_MIN = 54500.0
STOP_MAX = 60000.0


##########SERVO CONTROL##########

# Decrease for more RIGHT
SERVO_MIN = 1100

# Adjust for CENTER
SERVO_MID = 1450

# Increase for more LEFT
SERVO_MAX = 1500


#######POWER CONTROL########

# Drive power (0-255)
Power = 20


########################MAIN########################


#########VIDEO SOURCES#########

# tcap = cv2.VideoCapture('http://acecar.local:8080/?action=stream')  #For live video
# ocap = cv2.VideoCapture('http://acecar.local:8080/?action=stream')  #For live video
tcap = cv2.VideoCapture("C:/track.avi")  # Track detection video source
ocap = cv2.VideoCapture("C:/track.avi")  # Obstacle detection source


def map_range(x, in_min, in_max, out_min, out_max):
    return (x - in_min) * (out_max - out_min) // (in_max - in_min) + out_min


def obstacle_detection():

    # Global y axis value for obstacle detection
    global oby
    oby = 0

    # Obstacle color range
    low_b = np.uint8([5, 255, 255])
    high_b = np.uint8([0, 5, 2])

    while True:
        # Read the frames and store them in the frame variable
        Ret, frame = ocap.read()

        # Find the contours of the line
        mask = cv2.inRange(frame, high_b, low_b)

        kernel = np.ones((5, 5), np.uint8)  # Kernel for erosion and dilation
        mask = cv2.erode(mask, kernel, iterations=5)  # Erode to remove noise

        # Dilate to fill in the gaps
        mask = cv2.dilate(mask, kernel, iterations=9)

        # Find the contours chenaged from NONE to SIMPLE can check the number between -1 and 1
        contours, hierachy = cv2.findContours(mask, 1, cv2.CHAIN_APPROX_SIMPLE)
        if len(contours) > 0:

            c = max(contours, key=cv2.contourArea)
            M = cv2.moments(c)
            if M["m00"] != 0:

                obx = int(M['m10']/M['m00'])
                oby = int(M['m01']/M['m00'])
                #print(obx, " ", oby)

                # Make a cirlce at the center of the contour(x,y)
                cv2.circle(frame, (obx, oby), 5, (0, 0, 255), -1)

        # Draw the cotour of the line
        cv2.drawContours(frame, contours, -1, (0, 255, 0), 1)

        # Display the views
        #cv2.imshow("ObstacleMask", mask)
        cv2.imshow("ObstacleFrame", frame)

        # Stop the program if q key is pressed
        if cv2.waitKey(1) & keyboard.is_pressed('q'):
            ocap.release()
            cv2.destroyWindow("ObstacleFrame")
            break


def track_detection():

    # Center position in x axis (for track following)
    global cx
    cx = 0

    # Area of the contour (for end detection)
    global area
    area = 0

    # Track detection threashold
    high_b = np.uint8([255])
    low_b = np.uint8([8])

    while True:

        # Capture the frames and store them in the frame variable
        Ret, frame = tcap.read()

        # Convert the frames to gray scale
        frame = cv2.cvtColor(frame, cv2.COLOR_BGR2GRAY)

        # Cut off a part of the frame to not show too much
        frame = frame[0:360, 0:480]

        # Find the contours of the line
        mask = cv2.inRange(frame[150:360, 0:480], low_b, high_b)

        kernel = np.ones((6, 6), np.uint8)  # Kernel for erosion and dilation
        mask = cv2.erode(mask, kernel, iterations=5)  # Erode to remove noise

        # Dilate to fill in the gaps
        mask = cv2.dilate(mask, kernel, iterations=9)

        # Find the contours chenaged from NONE to SIMPLE can check the number between -1 and 1
        contours, hierachy = cv2.findContours(mask, 1, cv2.CHAIN_APPROX_SIMPLE)

        # If there is a contour do...
        if len(contours) > 0:

            # Find the biggest contour
            c = max(contours, key=cv2.contourArea)
            M = cv2.moments(c)
            #print((area := cv2.contourArea(c)))

            # If the contour is big enough do...
            if M["m00"] != 0:
                cx = int(M['m10']/M['m00'])
                cy = int(M['m01']/M['m00'])
                #print(cx," ", cy)

                # Make a cirlce at the center of the contour(x,y)
                cv2.circle(frame, (cx, cy), 5, (0, 0, 255), -1)

        # Draw the cotour of the line
        cv2.drawContours(frame, contours, -1, (0, 255, 0), 1)

        
        # Display the views
        cv2.imshow("TrackMask", mask)
        cv2.imshow("Outline", frame)

        # Stop if q is pressed
        if cv2.waitKey(1) & keyboard.is_pressed('q'):
            ocap.release()
            cv2.destroyWindow("TrackMask")
            cv2.destroyWindow("Outline")
            break


def control():

    # Connect to remote gpio with this hostname
    pi = pigpio.pi('acecar.local')

    # Set the required pins to output
    pi.set_mode(INA, pigpio.OUTPUT)
    pi.set_mode(INB, pigpio.OUTPUT)
    pi.set_mode(MotorPin, pigpio.OUTPUT)
    pi.set_mode(ServoPin, pigpio.OUTPUT)

    # Drive forward
    pi.set_PWM_dutycycle(MotorPin, Power)  # Power is PWM (from 0-255)
    pi.write(INA, 0)
    pi.write(INB, 1)

    while True:

        #####################STEEERING##############################

        # Attempt to implement proportional control for steering
        MappedVal = map_range(cx, CX_MIN, CX_MAX, SERVO_MIN, SERVO_MAX)
        ClippedVal = np.clip(MappedVal, SERVO_MIN, SERVO_MAX)
        pi.set_servo_pulsewidth(ServoPin, ClippedVal)
        print("servo:", ClippedVal, " cx:", cx)

        '''if cx < CX_MIN:
            #print("CX: " + str(cx) + " L")
            pi.set_servo_pulsewidth(ServoPin, SERVO_MAX)

        if cx > CX_MIN and cx < CX_MAX:
            #print("CX: " + str(cx) + " C")
            pi.set_servo_pulsewidth(ServoPin, SERVO_MID)

        if cx > CX_MAX:
            #print("CX: " + str(cx) + " R")
            pi.set_servo_pulsewidth(ServoPin, SERVO_MIN)'''

        #############OBSTACLE AVOIDANCE#############################
        '''if oby > OBY_MIN and oby < OBY_MAX:

            # Center wheels and drive backwards for 3 seconds
            pi.set_servo_pulsewidth(ServoPin, SERVO_MID)
            pi.write(INA, 1)
            pi.write(INB, 0)
            time.sleep(3)

            # Turn right and drive forward for 3 seconds
            pi.set_servo_pulsewidth(ServoPin, SERVO_MIN)
            pi.write(INA, 0)
            pi.write(INB, 1)
            time.sleep(1)
            # Turn left and continue with program
            pi.set_servo_pulsewidth(ServoPin, SERVO_MAX)'''

        ###########################END EXECUTION##############################
        if keyboard.is_pressed('q') or area >= STOP_MIN and area <= STOP_MAX:

            # Center the wheels and drive backards at 40 pwm for 0.2 seconds
            pi.set_servo_pulsewidth(ServoPin, SERVO_MID)
            pi.write(INA, 1)
            pi.write(INB, 0)
            pi.set_PWM_dutycycle(MotorPin, 40)
            time.sleep(0.2)

            # Brake the car for 0.2 seconds
            pi.set_PWM_dutycycle(MotorPin, 255)
            pi.write(INA, 1)
            pi.write(INB, 1)
            time.sleep(0.2)

            # Set all outputs to 0
            pi.set_PWM_dutycycle(MotorPin, 0)
            pi.write(INA, 0)
            pi.write(INB, 0)
            pi.stop()

            # Close the video sources and exit the loop
            ocap.relese()
            tcap.release()
            cv2.destroyAllWindows()
            break

#############################THREADS############################################


########TRACK DETECTION#######
t_trackdetection = threading.Thread(target=track_detection)
t_trackdetection.start()

#########OBSTACLE DETECTION#######
#t_obstacledetection = threading.Thread(target=obstacle_detection)
#t_obstacledetection.start()

#######CONTROL/STEERING######
t_control = threading.Thread(target=control)
# t_control.start()

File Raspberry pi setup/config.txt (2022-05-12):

# For more options and information see
# http://rpf.io/configtxt
# Some settings may impact device functionality. See link above for details

# uncomment if you get no picture on HDMI for a default "safe" mode
#hdmi_safe=1

# uncomment the following to adjust overscan. Use positive numbers if console
# goes off screen, and negative if there is too much border
#overscan_left=16
#overscan_right=16
#overscan_top=16
#overscan_bottom=16

# uncomment to force a console size. By default it will be display's size minus
# overscan.
#framebuffer_width=1280
#framebuffer_height=720

# uncomment if hdmi display is not detected and composite is being output
#hdmi_force_hotplug=1

# uncomment to force a specific HDMI mode (this will force VGA)
#hdmi_group=1
#hdmi_mode=1

# uncomment to force a HDMI mode rather than DVI. This can make audio work in
# DMT (computer monitor) modes
#hdmi_drive=2

# uncomment to increase signal to HDMI, if you have interference, blanking, or
# no display
#config_hdmi_boost=4

# uncomment for composite PAL
#sdtv_mode=2

#uncomment to overclock the arm. 700 MHz is the default.
#arm_freq=800

# Uncomment some or all of these to enable the optional hardware interfaces
#dtparam=i2c_arm=on
#dtparam=i2s=on
#dtparam=spi=on

# Uncomment this to enable infrared communication.
#dtoverlay=gpio-ir,gpio_pin=17
#dtoverlay=gpio-ir-tx,gpio_pin=18

# Additional overlays and parameters are documented /boot/overlays/README

# Enable audio (loads snd_bcm2835)
dtparam=audio=on

# Automatically load overlays for detected cameras
camera_auto_detect=1

# Automatically load overlays for detected DSI displays
display_auto_detect=1

# Enable DRM VC4 V3D driver
dtoverlay=vc4-kms-v3d
max_framebuffers=2

# Disable compensation for displays with overscan
disable_overscan=1

[cm4]
# Enable host mode on the 2711 built-in XHCI USB controller.
# This line should be removed if the legacy DWC2 controller is required
# (e.g. for USB device mode) or if USB support is not required.
otg_mode=1

[all]

[pi4]
# Run as fast as firmware / board allows
arm_boost=1

[all]
#dtoverlay=disable-wifi
#dtoverlay=disable-bt
dtoverlay=dwc2
#arm_freq=1095
#gpu_freq=550
#core_freq=515
#sdram_freq=533
#sdram_schmoo-0x02000020
#over_voltage=2
#over_voltage_sdram=2
#force_turbo=1
gpu_mem=128

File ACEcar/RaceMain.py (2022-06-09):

##########IMPORTS##########
import cv2
import time
import pigpio
import keyboard
import threading
import numpy as np


########OUTPUT PINS########

ServoPin = 13
MotorPin = 12
INA = 5
INB = 6


########MIN/MAX VALUES########

# Line following threshold
CX_MIN = 200
CX_MAX = 300


# Min/Max obstacle stop values
END_MIN = 180
END_MAX = 236


##########SERVO CONTROL##########

# Decrease for more RIGHT
SERVO_MIN = 1400

# Adjust for CENTER
SERVO_MID = 1428

# Increase for more LEFT
SERVO_MAX = 1456

#######POWER CONTROL########

# Drive power (0-255)
Power = 100


#########VIDEO SOURCES#########

#tcap = cv2.VideoCapture('http://acecar.local:8080/?action=stream')  #For live video
tcap = cv2.VideoCapture("C:/track.avi")  # Track detection video source


def map_range(x, in_min, in_max, out_min, out_max):
    return (x - in_min) * (out_max - out_min) // (in_max - in_min) + out_min


def track_detection():

    # Center position in x axis (for track following)
    global cx
    cx = 0

    # Area of the contours (for end detection)
    global area1
    area1 = 0

    global area2
    area2 = 0

    # Track detection threashold
    high_b = np.uint8([255])
    low_b = np.uint8([90])

    while True:

        # Capture the frames and store them in the frame variable
        Ret, frame = tcap.read()

        # Convert the frames to gray scale
        frame = cv2.cvtColor(frame, cv2.COLOR_BGR2GRAY)
        # Cut off a part of the frame to not show too much
        frame = frame[0:360, 0:480]
        frame = cv2.blur(frame, (5, 5))  # Blur the image to remove noise

        #create mask from threshold values
        mask = cv2.inRange(frame, low_b, high_b)
        kernel = np.ones((6, 6), np.uint8)  # Kernel for erosion and dilation
        mask = cv2.erode(mask, kernel, iterations=5)  # Erode to remove noise
        # Dilate to fill in the gaps
        mask = cv2.dilate(mask, kernel, iterations=9)
        # Find the contours in the mask
        contours, hierachy = cv2.findContours(mask, 1, cv2.CHAIN_APPROX_NONE)

        # If there is line tracking contour do...
        if len(contours) > 0:
            # Find the biggest contour
            c = max(contours, key=cv2.contourArea)
            M = cv2.moments(c)
            # If the contour is big enough do...
            if M["m00"] != 0:
                cx = int(M['m10']/M['m00'])
                cy = int(M['m01']/M['m00'])
                # Make a cirlce at the center of the contour(x,y)
                cv2.circle(frame, (cx, cy), 5, (0, 0, 255), -1)

        # find + filter contours for left side end detection
        emask1 = cv2.inRange(frame, low_b, high_b)
        emask1 = cv2.erode(emask1, kernel, iterations=5)
        emask1 = cv2.dilate(emask1, kernel, iterations=9)
        # cut cut off most of the frame
        emask1 = emask1[100:160, 0:5]
        e1contours, hierachy = cv2.findContours(emask1, 1, cv2.CHAIN_APPROX_NONE)

        # find +filter contours for right side end detection
        emask2 = cv2.inRange(frame, low_b, high_b)
        emask2 = cv2.erode(emask2, kernel, iterations=5)
        emask2 = cv2.dilate(emask2, kernel, iterations=9)
        # cut off most of the frame
        emask2 = emask2[100:160, 475:480]
        e2contours, hierachy = cv2.findContours(emask2, 1, cv2.CHAIN_APPROX_NONE)

        # If there is contour e1 do...
        if len(e1contours) > 0:
            ec1 = max(e1contours, key=cv2.contourArea)
            area1 = cv2.contourArea(ec1)
            print(area1, "L")
        else:
            area1 = 0

        # If there is contour e2 do...
        if len(e2contours) > 0:
            ec2 = max(e2contours, key=cv2.contourArea)
            area2 = cv2.contourArea(ec2)
            print(area2, "R")
        else:
            area2 = 0

        # Draw the cotour of the line
        cv2.drawContours(frame, contours, -1, (0, 255, 0), 1)

        # Display the views
        #cv2.imshow("TrackMask", mask)
        cv2.imshow("Outline", frame)
        cv2.imshow("emask1", emask1)
        cv2.imshow("emask2", emask2)
        cv2.waitKey(1)
        if keyboard.is_pressed('q'):
            print("MANUAL STOP ON TRACK DETECTION")
            break

        if area1 >= END_MIN and area1 <= END_MAX and area2 >= END_MIN and area2 <= END_MAX:
            print("END EXECUTION ON TRACK DETECTION SUCCESS")
            break


def control():

    # Connect to remote gpio with this hostname
    pi = pigpio.pi('acecar.local')

    # Set the required pins to output
    pi.set_mode(INA, pigpio.OUTPUT)
    pi.set_mode(INB, pigpio.OUTPUT)
    pi.set_mode(MotorPin, pigpio.OUTPUT)
    pi.set_mode(ServoPin, pigpio.OUTPUT)

    # Drive forward
    pi.set_PWM_dutycycle(MotorPin, Power)  # Power is PWM (from 0-255)
    pi.set_servo_pulsewidth(ServoPin, SERVO_MID)  # Set the servo to center

    pi.write(INA, 0)
    pi.write(INB, 1)

    while True:

        #####################STEEERING##############################

        MappedVal = map_range(cx, CX_MAX, CX_MIN, SERVO_MIN, SERVO_MAX)
        ClippedVal = np.clip(MappedVal, SERVO_MIN, SERVO_MAX)
        pi.set_servo_pulsewidth(ServoPin, ClippedVal)
        #print("servo:", ClippedVal, " cx:", cx)

        ###########################END EXECUTION##############################
        if keyboard.is_pressed('space'):
            print("EMERGENCY STOP ON CONTROL")
            pi.set_servo_pulsewidth(ServoPin, SERVO_MID)
            pi.write(INA, 1)
            pi.write(INB, 0)
            pi.set_PWM_dutycycle(MotorPin, 40)
            time.sleep(1)
            # Stop the car and clean up
            pi.set_PWM_dutycycle(MotorPin, 0)
            pi.write(INA, 0)
            pi.write(INB, 0)
            pi.stop()
            break

        if area1 >= END_MIN and area1 <= END_MAX and area2 >= END_MIN and area2 <= END_MAX:
            print("END EXECUTION ON CONTROL SUCCESS")
            # Center the wheels and drive backards at 40 pwm for x seconds
            pi.set_servo_pulsewidth(ServoPin, SERVO_MID)
            pi.write(INA, 1)
            pi.write(INB, 0)
            pi.set_PWM_dutycycle(MotorPin, 0)
            time.sleep(0.7)
            # Stop the car and clean up
            pi.set_PWM_dutycycle(MotorPin, 0)
            pi.write(INA, 0)
            pi.write(INB, 0)
            pi.stop()
            break

#############################THREADS############################################


########TRACK DETECTION#######
t_trackdetection = threading.Thread(target=track_detection)
t_trackdetection.start()

#######CONTROL/STEERING######
t_control = threading.Thread(target=control)
# t_control.start()

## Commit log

2022-05-12 Added a bunch of test files & documentation & stuff + other
    [ACEcar.PrjPcb, Header.PcbLib, Header.SchLib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]
2022-05-17 Added keyboard control code to main code and tested on prototype
2022-05-17 Lil changes
    [Sheet1.SchDoc]
2022-05-20 Added servo and motor control code
    [Sheet1.SchDoc]
2022-05-20 Changed voltage divider resistance values
2022-05-20 changed voltage divider resistane values
    [Sheet1.SchDoc]
2022-05-20 Protomain now file for prototype car
2022-05-20 ProtoMain now name for prototype car code
2022-05-20 POG Working line following implementation (Not very good but works) (last commit had wrong message)
    [ProtoMain.py]
2022-05-31 Add more filters and change some data with all calibration for testing
2022-06-01 Adjusted line detection and steering thresholds seems to work much better now
2022-06-02 added base code for obstacle avoidane
    [Main.py]
2022-06-06 Added pin configuration to README.md
    https://github.com/karolis1115/ACEcar/edit/master/README.md#raspberry-pi-pin-configuration
2022-06-06 Added Missing documentation
    [ACEcar Bestelformulier-Orderform.xlsm, ACEcar Log book.xlsx, AceCar gantt chart.xlsx]
2022-06-07 Added attemt to implement proportional steering
2022-06-10 Fixed typos on silkscreen
    [PCB1.PcbDoc]
2022-09-06 Finall commit (For now atleast)
    [Back car.3mf, Front car.3mf, Split car.3mf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]
